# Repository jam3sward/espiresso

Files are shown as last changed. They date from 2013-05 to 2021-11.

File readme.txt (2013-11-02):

Starting the controller
-----------------------

sudo /etc/init.d/gaggia start

Stopping the controller
-----------------------

The halt button should be pushed to provide an opportunity for the PI to
shutdown before removing mains power.

sudo /etc/init.d/gaggia stop

Configuration files
-------------------

/etc/gaggia.conf

Data files
----------

Data is recorded to:
/var/log/gaggia/

Each run results in a new CSV (Comma Separated Values) file which is named
with the start date and time as follows:
YYMMDD-HHMM.csv

There is no upper limit on the number or size of these files, so they need
to be cleaned up manually. The files are fairly small (even if the machine
is left on for a couple of hours, the file would only be around 180kb).

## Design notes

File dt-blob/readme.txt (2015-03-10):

Step 1: check that Raspberry Pi firmware is later than July 15th 2014
---------------------------------------------------------------------

vcgencmd version

Step 2: install device tree compiler
------------------------------------

sudo apt-get update
sudo apt-get install device-tree-compiler

Step 3: edit the device tree source file as needed
--------------------------------------------------

nano dt-blob.dts

Step 4: compile the device tree source file to binary blob
----------------------------------------------------------

sudo dtc -I dts -O dtb -o /boot/dt-blob.bin dt-blob.dts

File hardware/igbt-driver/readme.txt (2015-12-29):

Eagle Schematic and Board files
The CAM files are in the pcb-cam-v1 folder

J.Ward
27/02/15

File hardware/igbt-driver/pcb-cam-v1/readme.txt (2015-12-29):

Es(pi)resso IGBT Driver

CAM files for PCB manufacture
Version: V1
Created: 27/02/15

These same files were used to successfully
manufacture a single prototype PCB here:
http://www.ragworm.eu

J.Ward
27/02/15

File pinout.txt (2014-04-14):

 3. GPIO2  = Button 1 (BUTTON1)
 5. GPIO3  = Button 2 (BUTTON2)
 7. GPIO4  = DS18B20 Thermometer (TEMPERATURE_BUS)
12. GPIO18 = SSR (SSR_OUT)
13. GPIO27 = Flow Sensor (FLOW_IN)
15. GPIO22 = Ultrasonic Ranger Echo In (RANGER_ECHO_IN)
16. GPIO23 = Ultrasonic Ranger Trigger Out (RANGER_TRIGGER_OUT)
18. GPIO24 = TSIC306 Temperature Sensor (TEMPERATURE_TSIC1)

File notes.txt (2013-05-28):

Running at startup
------------------
Created a script at:
/etc/init.d/gaggia

This starts automatically at boot, and stops at shutdown.

Manually start/stop as follows:
sudo /etc/init.d/gaggia start
sudo /etc/init.d/gaggia stop

Binary location
---------------
The binary is located here:
/usr/local/bin/gaggia

Logging
-------
Temperature logs are stored here:
/var/log/gaggia
Files are stored in CSV format.
File names are based on date and time.

Issues
------
* Time/date are incorrect when run from init.d (locale issue?)
* Discontinuous jumps in time stamps (probably due to NTP adjustment)

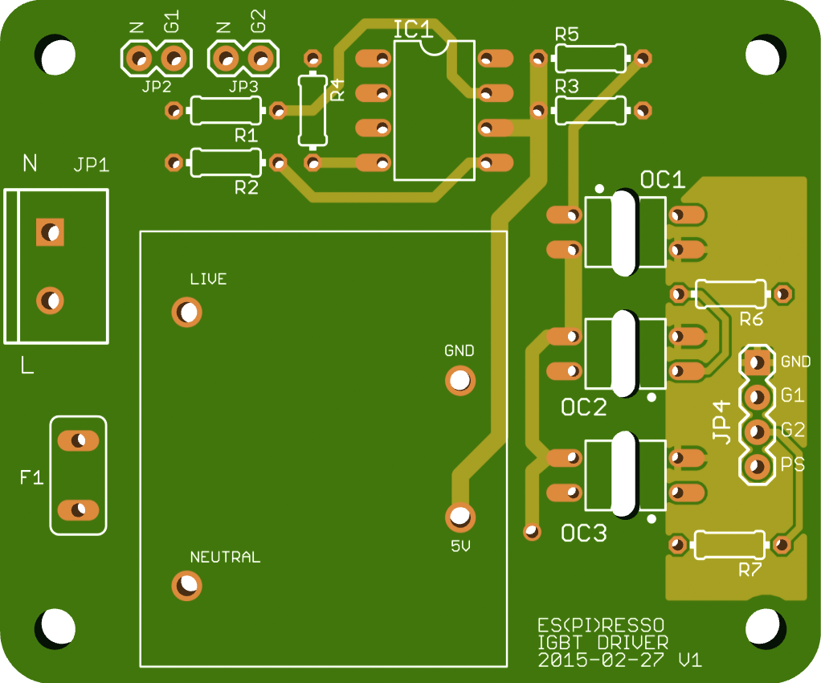
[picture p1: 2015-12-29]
hardware/igbt-driver/pcb-cam-v1/picture.png

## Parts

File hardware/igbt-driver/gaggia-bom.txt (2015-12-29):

Part Value           Device          Package             Description                              MF MPN OC_FARNELL OC_NEWARK
F1   1A              FUSETE5         TE5                 Fuse                                            unknown    unknown  
IC1  TC426           TC426           DIL08               1.5A Dual High-Speed Power MOSFET Driver                            
JP1  POWER           M025MM          SCREWTERMINAL-5MM-2 Standard 2-pin 0.1" header.                             
JP2  IGBT1           M02PTH          1X02                Standard 2-pin 0.1" header.                               
JP3  IGBT2           M02PTH          1X02                Standard 2-pin 0.1" header.                               
JP4  CONTROL         M04PTH          1X04                Standard 4-pin 0.1" header.                                                       
OC1  HCPL-817        TIL197          DIL04               TEXAS INSTRUMENTS OPTO COUPLER                  1683368    unknown  
OC2  HCPL-817        TIL197          DIL04               TEXAS INSTRUMENTS OPTO COUPLER                  1683368    unknown  
OC3  HCPL-817        TIL197          DIL04               TEXAS INSTRUMENTS OPTO COUPLER                  1683368    unknown  
R1   1K              R-EU_0204/7     0204/7              RESISTOR                                          
R2   1K              R-EU_0204/7     0204/7              RESISTOR                                         
R3   4K7             R-EU_0204/7     0204/7              RESISTOR                                           
R4   4K7             R-EU_0204/7     0204/7              RESISTOR                                           
R5   360R            R-EU_0204/7     0204/7              RESISTOR                                           
R6   270R            R-EU_0204/7     0204/7              RESISTOR                                           
R7   270R            R-EU_0204/7     0204/7              RESISTOR                                           
RG1  VTX-214-003-105 VTX-214-003-105 VTX-214-003         Vigortronix 90-265V AC to 5V DC 600mA

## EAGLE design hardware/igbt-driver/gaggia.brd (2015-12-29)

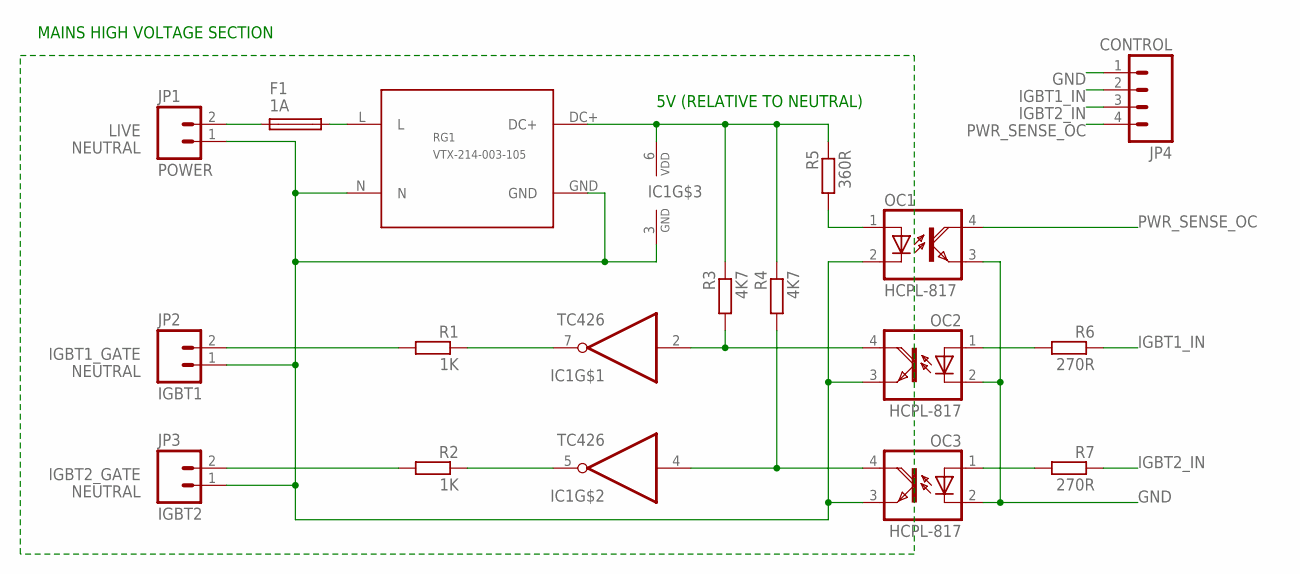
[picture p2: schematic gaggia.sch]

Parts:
F1: 1A; TE5
IC1: TC426; DIL08
JP1: POWER; SCREWTERMINAL-5MM-2
JP2: IGBT1; 1X02
JP3: IGBT2; 1X02
JP4: CONTROL; 1X04
OC1, OC2, OC3: HCPL-817; DIL04
R1, R2: 1K; 0204/7
R3, R4: 4K7; 0204/7
R5: 360R; 0204/7
R6, R7: 270R; 0204/7
RG1: VTX-214-003-105; VTX-214-003

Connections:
5V_NON_ISOLATED: IC1.6 (VDD), R3.1, R4.1, R5.1, RG1.DC+
GND: JP4.1, OC1.3 (EMI), OC2.2 (C), OC3.2 (C)
IGBT1_GATE: JP2.2, R1.2
IGBT1_IN: JP4.2, R6.1
IGBT2_GATE: JP3.2, R2.2
IGBT2_IN: JP4.3, R7.1
LIVE: F1.1, JP1.2
unnamed: IC1.4 (I), OC3.4 (COL), R4.2
unnamed: IC1.5 (O), R2.1
unnamed: OC3.1 (A), R7.2
unnamed: IC1.7 (O), R1.1
unnamed: OC1.1 (A), R5.2
unnamed: OC2.1 (A), R6.2
unnamed: IC1.2 (I), OC2.4 (COL), R3.2
unnamed: F1.2, RG1.L
NEUTRAL: IC1.3 (GND), JP1.1, JP2.1, JP3.1, OC1.2 (C), OC2.3 (EMI), OC3.3 (EMI), RG1.GND, RG1.N
PWR_SENSE_OC: JP4.4, OC1.4 (COL)

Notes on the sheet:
MAINS HIGH VOLTAGE SECTION
5V (RELATIVE TO NEUTRAL)

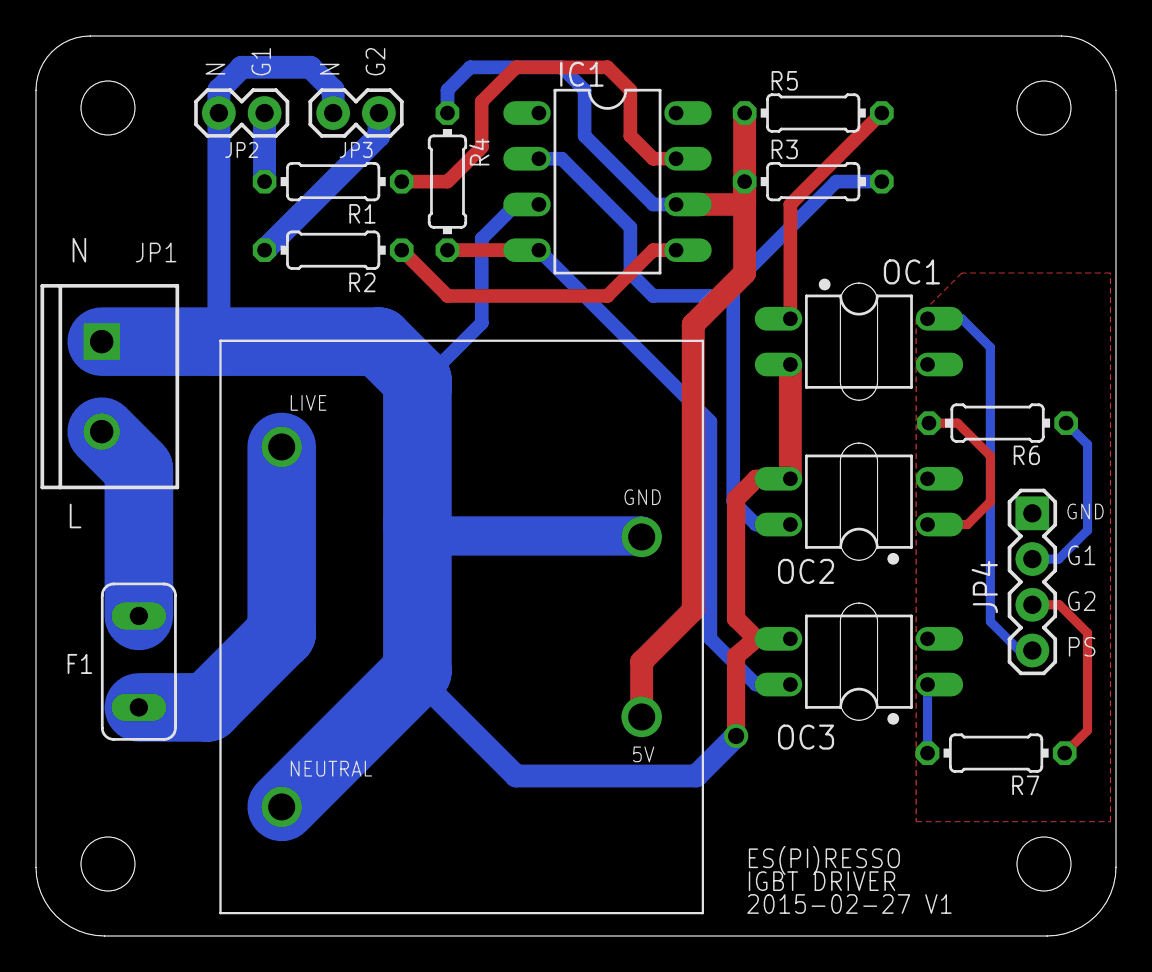
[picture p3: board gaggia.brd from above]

Board: 2 copper layers, 60.0 x 50.0 mm, 17 parts (0 on the bottom side), 17 nets.

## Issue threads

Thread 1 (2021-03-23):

Porting to the La Pavoni Puccino PCL

darkbasic, 2021-03-23:
Hi, first of all let me say "wow", you've put so much effort in this and ended up being such a great project!
I would like to port it to the La Pavoni Puccino PCL, but I'd like to start with the basics and eventually expand it later.
For the first iteration I'd like to implement only temperature control: no pump control, nor pressure, flow or water level.
I'm not a C++ developer (but I'm a Linux enthusiast) so I'll need some help to strip out the code base and test the individual pieces. Would you be willing to help me? I'm not sure if this is the right place to ask, but I didn't find any public email address.

jam3sward, 2021-03-24:
Thanks for the kind words!
Sure, would be happy to help with the odd question. The temperature control is where 99% of the benefit is to be had, so a good place to start!
Honestly speaking, although I implemented pump control and my machine can dispense a measured volume using its flow sensor... I still tend to just manually turn the pump on/off when pulling my morning shots :)
The water level sensor is really handy though, I find that really useful when topping up the machine.
I'm not sure how either of us can exchange e-mail addresses on here without exposing them to spammers, so I'm going to suggest you post on my blog here (which will reveal your e-mail address to me, then I can reply): http://int03.co.uk/blog/

darkbasic, 2021-03-24:
Awesome, I think I've managed to find your email address (and I've sent you an email), but I've also posted a comment to your blog just to be sure.

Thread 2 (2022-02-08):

Sorry, not an issue

SpeedGP, 2022-02-08:
Dude, you rock, this is crazy and exactly what I was looking for!!!

Any reason you're not running this on an Arduino instead? Seems like less can go wrong when you're not running a full OS.

Are you concerned about redundancy with the thermostat? I would like to see a temp fuse or is that what the pressure sensor is for? - pressure vessels scare the absolute crap out of me....

I'm planning a bare-bones mod, probably only PID and time monitoring. I think a scale mod of some sort would be cool, but probably difficult.

Thanks again for all of the time, dev, and love of coffee!!!

jam3sward, 2022-02-19:
Thanks for the kind words! Sorry it took a while to reply... I've only just spotted this.

I did consider Arduino, and it would be a good choice too. There are pros and cons of each, it depends how you plan to use it:
* Boot up time: Raspi takes a while to boot up, Arduino would be instant! (Arduino wins here)
* Remote access: Raspi means you can log in remotely, update the code over the network, have a Samba share with temperature/pressure logs... none of which is easy with Arduino. (Raspis wins here)
* I/O: sadly the Raspi has no analogue inputs, and needs an external ADC. The Arduino has plenty of course. (Arduino wins here)

So, if you don't care about being able to remotely log in and tinker with the code, or share logs on the network etc, then Arduino would be a very good choice of course!

Regarding redundancy with the thermostat, the Gaggia Classic has a thermal fuse (and it is still in circuit in my setup, as is the steam thermostat). So, if my temperature sensor fails or the software crashes, the first thing to open would be the steam thermostat. If the steam thermostat fails, the thermal fuse is next. So it has plenty of redundancy I would say.

Good luck with your project! The main benefit is the PID temperature control. That alone is enough to yield an amazing improvement in the quality of your espresso :)

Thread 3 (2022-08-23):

Boiler control

moosepr, 2022-08-23:
Hi there

I stumbled upon your project when looking into variable pressure control of coffee machine pumps and it's literally everything I had ever dreamed of! Truly fantastic work!

I would like to do something similar with an esp32 for brains, and was hoping i could make an all in one PCB to simplify the install.

I'm by no means an electrical engineer, but I can cut and paste a few circuits together with moderate success.

If you were doing it all again, would you use an IGBT to control the boiler as well as the pump? Your custom PCB has the spare channel available, it would be easy enough to add it in

Thanks

Pete

jam3sward, 2023-01-12:
I'm ashamed to reply to this after so long, but I just didn't see the notification!

Thanks for the kind words above, I'm pleased to hear that you found it helpful, and guess you must be well along with your ESP32 project by now :)

If I did this again, I would probably still use the SSR to switch the boiler, perhaps even the exact same model. There's so much thermal mass in the boiler and it is slow to react to input, so I think there is no advantage to high speed switching for that application and low speed PWM control is more than adequate to regulate boiler temperature.

On the other hand, I have come to think that the high speed IGBT switching of the pump is overkill and I would do that differently and more simply in a V2 design.

moosepr, 2023-01-20:
dont be ashamed!! its all good my project is still just an idea!!

I had been thinking of using a SSR for the pump, cycling it a few times a second would let you reduce the pressure without needing to get all precise with the cycle timing.

that being said, i was looking at making a custom pcb with it all baked in (not much space inside my machine) and pcb mounted SSR's are silly money!!

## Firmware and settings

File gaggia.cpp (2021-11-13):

#include <stdio.h>
#include <sched.h>
#include <ctype.h>
#include <signal.h>
#include <unistd.h>
#include <string>
#include <iostream>
#include <fstream>
#include <sstream>
#include <map>
#include <memory>

#include "timing.h"
#include "regulator.h"
#include "flow.h"
#include "pump.h"
#include "ranger.h"
#include "keyboard.h"
#include "inputs.h"
#include "system.h"
#include "display.h"
#include "adc.h"
#include "pressure.h"
#include "settings.h"
#include "pigpiomgr.h"
#include "network.h"

using namespace std;

//-----------------------------------------------------------------------------

static const string filePath( "/var/log/gaggia/" );
static const string configFile( "/etc/gaggia.conf" );

//-----------------------------------------------------------------------------

std::map<std::string, double> config;

bool g_enableBoiler = true;	///< Enable boiler if true
bool g_quit = false;		///< Should we quit?
bool g_halt = false;        ///< Should we halt? (shutdown the system)

double g_shotSize = 60.0;   ///< Shot size in ml

/// Automatic power off time in seconds. Zero disables the time out.
double g_autoPowerOff = 0.0;

class Hardware {
private:
    Timer       m_lastUsed;     ///< When was the last user interaction?
    ADC         m_adc;          ///< ADC used for buttons and pressure sensor
    Pump        m_pump;         ///< Pump controller
    Flow        m_flow;         ///< Flow sensor to measure volume dispensed
    Temperature m_temperature;  ///< Boiler temperature sensor
    Ranger      m_ranger;       ///< Range finder to measure water level
    Display     m_display;      ///< LCD display screen
    System      m_system;       ///< System information
    bool        m_pumpSense;    ///< Is the pump active?
    unsigned    m_pourCount;    ///< Pour count
    Timer       m_pourTime;     ///< Pour timer
    std::string m_networkIP;    ///< Primary network IP address

    std::shared_ptr<Regulator> m_regulator;

    std::shared_ptr<Inputs> m_inputs;

    std::shared_ptr<Pressure> m_pressure;

public:
    Timer & lastUsed() { return m_lastUsed; }

    ADC & adc() { return m_adc; }

    Pump & pump() { return m_pump; }

    Flow & flow() { return m_flow; }

    Temperature & temperature() { return m_temperature; }

    Ranger & ranger() { return m_ranger; }

    Display & display() { return m_display; }

    System & system() { return m_system; }

    Regulator & regulator() { return *m_regulator; }

    Inputs & inputs() { return *m_inputs; }

    Pressure & pressure() { return *m_pressure; }

    /// Returns true if the pump is active (whether enabled in software, or by
    /// using the manual front panel switch)
    bool pumpSense() const { return m_pumpSense; }

    /// Returns the pour counter value
    unsigned pourCount() const { return m_pourCount; }

    /// Returns the pour time in seconds
    double pourTime() const;

    /// Constructor
    Hardware() {
        // reset and stop the timer
        m_pourTime.reset().stop();

        // used to sense when pump is running
        m_pumpSense = false;

        // used to count how many times the pump has run
        m_pourCount = 0;

        // initialise ADC
        if ( !m_adc.open( I2C_DEVICE_PATH, ADS1015_ADC_I2C_ADDRESS ) )
            cerr << "gaggia: failed to open ADC\n";

        m_regulator = std::make_shared<Regulator>( m_temperature );
        m_inputs = std::make_shared<Inputs>( m_adc, ADC_BUTTON_CHANNEL );
        m_pressure = std::make_shared<Pressure>( m_adc, ADC_PRESSURE_CHANNEL );

        using namespace std::placeholders;

        // register button handler
        inputs().notifyRegister(
            std::bind( &Hardware::buttonHandler, this, _1, _2, _3 )
        );

        // register flow notification handler
        flow().notifyRegister(
            std::bind( &Hardware::flowHandler, this, _1 )
        );
    }

    /// Destructor
    virtual ~Hardware() {
        m_inputs.reset();
        m_regulator.reset();
        m_pressure.reset();
    }

    /// Called when buttons are pressed or released
    void buttonHandler(
        int button,     // button number (1,2)
        bool state,     // pressed (true) or released (false)
        double time     // time period since last state change
    );

    /// Called when notifications are received from the flow sensor
    void flowHandler( Flow::NotifyType type );

    /// Run the control loop
    int runController(
	    bool interactive,
	    const std::string & fileName
    );

    /// Run test mode
    int runTests();
};

//-----------------------------------------------------------------------------

void signalHandler( int signal )
{
	switch ( signal ) {
	case SIGINT:
		printf( "\ngaggia: received SIGINT\n" );
		g_quit = true;
		break;

	case SIGTERM:
		printf( "\ngaggia: received SIGTERM\n" );
		g_quit = true;
		break;
	}
}

//-----------------------------------------------------------------------------

double Hardware::pourTime() const
{
    return m_pourTime.getElapsed();
}

//-----------------------------------------------------------------------------

/// Called when buttons are pressed or released
void Hardware::buttonHandler(
    int button,     // button number (1,2)
    bool state,     // pressed (true) or released (false)
    double time     // time period since last state change
) {
    // reset the timer whenever the user interacts with the machine
    lastUsed().reset();

    switch ( button ) {
    case BREW_SWITCH:
        // brew switch pushed
        // When the front panel brew switch is pushed to enable the pump, this
        // will be triggered. Since we detect this from the 5V supply in the
        // pump modulation controller, there will be a delay in detecting when
        // the pump is switched off (because the reservoir capacitor in the 5V
        // supply takes time to discharge)
        cout << "gaggia: brew switch "
             << (state ? "enabled" : "disabled")
             << endl;

        // set or clear the flag (stores current state)
        m_pumpSense = state;

        // start or stop the pour timer
        if ( state )
            m_pourTime.start();
        else
            m_pourTime.stop();

        // if the power has been enabled, increment the pour counter
        if ( state ) ++m_pourCount;

        break;

    case BUTTON1:
        if ( state ) {
            // button 1 pushed

            // if the pump is idle
            if ( !pump().getState() ) {
                // ask the flow sensor to notify us after a shot
                // has been dispensed
                flow().notifyAfter( g_shotSize / 1000.0 );
                // turn on the pump
                pump().setState( true );
            } else {
                // pump is already running: turn it off
                pump().setState( false );
            }

            // display pump status for diagnostic purposes
            cout << "gaggia: pump "
                 << (pump().getState() ? "enabled" : "disabled")
                 << endl;
        } else {
            // button 1 released
        }
        break;

    case BUTTON2:
        if ( state ) {
            // button 2 pushed
        } else {
            // button 2 released
            if ( time >= 1.0 ) {
                // button was held for 1 second, shut down the system
                cout << "gaggia: shutting down\n";
                g_halt = true;
                g_quit = true;
            } else {
                // button was pushed briefly, toggle boiler power
                regulator().setPower( !regulator().getPower() );
                cout << "gaggia: boiler "
                     << (regulator().getPower() ? "enabled" : "disabled")
                     << endl;
            }
        }
        break;
    }
}

//-----------------------------------------------------------------------------

/// Called when notifications are received from the flow sensor
void Hardware::flowHandler( Flow::NotifyType type ) {
    // reset the timer when the pump is used (e.g. via front panel switch)
    lastUsed().reset();

	switch ( type ) {
	case Flow::Start :
		cout << "flow: started\n";
		break;

	case Flow::Stop  :
		cout << "flow: stopped\n";
		break;

	case Flow::Target:
		cout << "flow: target reached\n";
        // stop the pump
        pump().setState( false );
		break;
	}
}

//-----------------------------------------------------------------------------

/// very simplistic configuration file loader
bool loadConfig( std::string fileName )
{
	// open the file
	ifstream f( fileName.c_str() );
	if ( !f ) return false;

	do {
		// read key
		string key;
		f >> ws >> key;
		if ( !f ) break;

		// read value
		double value;
		f >> ws >> value;
		if ( !f ) break;

		// store key/value
		config[key] = value;
		//cout << key << " = " << value << endl;
	} while (true);

	f.close();

	return true;
}

//-----------------------------------------------------------------------------

std::string makeLogFileName()
{
	// get the time
	time_t now;
	time( &now );
	struct tm *info = localtime( &now );

	// format date and time into the filename
	char buffer[256];
	sprintf(
		buffer,
		"%02d%02d%02d-%02d%02d.csv",
		info->tm_year % 100,
		info->tm_mon+1,
		info->tm_mday,
		info->tm_hour,
		info->tm_min
	);

	// return the string
	return buffer;
}

//-----------------------------------------------------------------------------

int Hardware::runController(
	bool interactive,
	const std::string & fileName
) {
    // if button 2 is pushed during initialisation, abort
    if ( inputs().getButton(2) ) {
        cerr << "gaggia: button 2 is down: aborting" << endl;
        return 1;
    }

	// open log file
	ofstream out( fileName.c_str() );
	if ( !out ) {
		cerr << "error: unable to open log file " << fileName << endl;
		return 1;
	}

	// check that flow meter is available
	if ( !flow().ready() ) {
		out << "error: flow meter not ready\n";
		return 1;
	}

	// read configuration file
	if ( !loadConfig( configFile ) ) {
		out << "error: failed to load configuration from "
			<< configFile << endl;
		return 1;
	}

    // shot size in millilitres
    g_shotSize = config["shotSize"];

    // read auto cut out time (the value in the file is in minutes,
    // and we convert to seconds here)
    g_autoPowerOff = config["autoPowerOff"] * 60.0;

	// read PID controller parameters from configuration
	// these are the proportional, integral, derivate coefficients and
	// the integrator limits
	const double kP = config["kP"];
	const double kI = config["kI"];
	const double kD = config["kD"];
	const double kMin = config["iMin"];
	const double kMax = config["iMax"];

	// set the PID controller parameters
	regulator().setPIDGains( kP, kI, kD );
	regulator().setIntegratorLimits( kMin, kMax );

	// target temperature in degrees centigrade
	double targetTemp = config["targetTemp"];
	regulator().setTargetTemperature( targetTemp );

	// time step in seconds
	double timeStep = config["timeStep"];
	regulator().setTimeStep( timeStep );

    // pressure sensor calibration
    {
        // these are the multiplier and offset used to calibrate the analogue pressure
        // transducer measurement to match the front panel mechanical pressure gauge
        const double scale = config["pressureScale"];
        const double offset = config["pressureOffset"];
        pressure().setCorrection( scale, offset );
    }

	// output parameters to log
	char buffer[512];
	sprintf(
		buffer,
		"P=%.4lf,I=%.4lf,D=%.4lf,iMin=%.3lf,iMax=%.3lf,"
		"targetTemp=%.3lf,timeStep=%.3lf",
		kP, kI, kD, kMin, kMax,
		targetTemp, timeStep
	);
	out << buffer << endl;

	if ( interactive )
		nonblock(1);

	// time step for user interface / display
	const double timeStepGUI = 0.25;

	// start time and next time step
	double start = getClock();
	double next  = start;

	// turn on the power and start the regulator (boiler will begin to heat)
	regulator().setPower( g_enableBoiler ).start();

	do {
		// next time step
		next += timeStepGUI;

		// in interactive mode, exit if any key is pressed
		if ( interactive && kbhit() ) break;

		// if asked to stop (e.g. via SIGINT)
		if ( g_quit ) break;

		// calculate elapsed time
		double elapsed = getClock() - start;

		// get the latest temperature reading
		double latestTemp = regulator().getTemperature();

		// get the latest boiler power level
		double powerLevel = regulator().getPowerLevel();

		// number of millilitres of water drawn up by the pump
		double ml = 1000.0 * flow().getLitres();

        // pressure in Bar
        double bar = pressure().getBar();

        // pump status
        int pump = pumpSense() ? 1 : 0;

        // pour number (zero if the pump isn't running)
        int pour = (pump > 0) ? pourCount() : 0;

		// dump values to log file
		sprintf(
			buffer,
			"%.3lf,%.2lf,%.2lf,%.1lf,%.2lf,%d,%d",
			elapsed, powerLevel, latestTemp, ml, bar, pump, pour
		);
		out << buffer << endl;

		if (interactive) {
			printf( "%.2lf %.2lf %.1lf %.2lf %d\n", elapsed, latestTemp, ml, bar, pour );
		}

		// update temperature display
		display().updateTemperature( latestTemp );

        // update pressure display
        display().updatePressure( bar );

        // range measurement (convert to mm)
        double range = 1000.0 * ranger().getRange();

		// simplistic conversion to water level
		double minDist = 20.0;
		double maxDist = 100.0;
		range = std::max( minDist, std::min( range, maxDist ) );
		double level = 1.0 - (range - minDist) / (maxDist - minDist);

		// update water level display
		display().updateLevel( level );

        // update boiler power indicator
        display().setPowerOn( regulator().getPower() );

        // update pump status indicator
        display().setPumpOn( pumpSense() );

        // update time display
        display().updateTime( pourTime() );

        // update the network status display
        if ( m_networkIP.empty() ) {
            // query IP address (may return empty string)
            m_networkIP = getPrimaryIPString();

            // update the display (string may be empty)
            if ( !m_networkIP.empty() ) {
                display().setMessage( m_networkIP );
            } else {
                display().setMessage( "no network" );
            }
        }

        // if auto cut out is enabled (greater than one second) and if too
        // much time has elapsed since the last user interaction, and the
        // timer is running, turn off the boiler as a precaution
        if (
            (g_autoPowerOff > 1.0) &&
            lastUsed().isRunning() &&
            (lastUsed().getElapsed() > g_autoPowerOff)
        ) {
            // switch off the boiler
            regulator().setPower( false );

            // stop the timer to prevent repeat triggering
            lastUsed().stop();

            // explanatory message
            cout << "gaggia: switched off power due to inactivity\n";
        }

		// sleep for remainder of time step
		double remain = next - getClock();;
		if ( remain > 0.0 )
			delayms( static_cast<int>(1.0E3 * remain) );
	} while (true);

	if ( interactive )
		nonblock(0);

	// turn the boiler off before we exit
	regulator().setPower( false );

    // if the halt button was pushed, halt the system
    if ( g_halt ) {
        // rather than shutting down immediately, we want to schedule this to
        // happen a few seconds after our process has exited. here we use
        // bash to run a background job which will sleep for a few seconds
        // before powering off the system

        // format the command string (including time in seconds)
        const auto shutdownDelay = static_cast<int>(config["shutdownDelay"]);
        stringstream command;
        command << "bash -c \"sleep " << shutdownDelay << "; poweroff \" &";

        // execute the comamnd
        ::system( command.str().c_str() );
    }

    // exit normally
    cerr << "gaggia: exiting controller\n";
    return 0;
}

//-----------------------------------------------------------------------------

int Hardware::runTests()
{
    cout << "flow: " <<
        (flow().ready() ? "ready" : "not ready")
        << endl;

    double degrees = 0.0;
    cout << "temp: " <<
        ( temperature().getDegrees(degrees) ? "ready" : "not ready")
        << endl;

	cout << "range: " <<
		( ranger().initialise() ? "ready" : "not ready" )
		<< endl;

	flow().notifyAfter( g_shotSize / 1000.0 );

    nonblock(1);

	// time step
	const double timeStep = 0.5;

	// start time and next time step
	double start = getClock();
	double next  = start;

    do {
        // calculate next time step
        next += timeStep;

		// if quit has been requested (e.g. via SIGINT)
		if ( g_quit ) break;

        if ( kbhit() ) {
			// get key
			char key = getchar();

            if ( ( key >= '0' ) && ( key <= '9' ) ) {
                int value = key - '0';
                if ( value > 0 ) {
                    double duty = static_cast<double>(value) / 10.0;
                    pump().setPWMDuty( duty );
                    pump().setState( true );
                    cout << "pump duty = " << duty << endl;
                } else
                    pump().setState( false );
                continue;
            }

			bool stop = false;
			switch ( tolower(key) ) {
			case 'p':
                if ( !pump().getState() ) {
                    flow().notifyAfter( 60.0 / 1000.0 );
                }
                pump().setPWMDuty( 1.0 );
				pump().setState( !pump().getState() );
				cout << "pump: " << (pump().getState() ? "on" : "off") << endl;
				break;

            case 'r':
                {
                    double range = 0.0;
                    const int count = 50;
                    for (int i=0; i<count; ++i)
                        range += ranger().getRange() * 1000.0;
                    cout << "range average: "
                         << range / static_cast<double>(count) << endl;
                }
                break;

			default:
				stop = true;
			}

			if (stop) break;
		}

        // read temperature sensor
        double temp = 0.0;
        temperature().getDegrees( temp );

        // read core temperature
        double coreTemp = system().getCoreTemperature();

        // number of millilitres of water drawn up by the pump
        double ml = 1000.0 * flow().getLitres();

        // range measurement (convert to mm)
        double range = 1000.0 * ranger().getRange();

        // pressure measurement
        double bar = pressure().getBar();

        // print sensor values
        printf(
			"%.2lfC %.2lfC %.1lfml %.0lfmm %.1lf\n",
			temp, coreTemp, ml, range, bar
		);

		// update temperature on display
		display().updateTemperature( temp );

		// sleep for remainder of time step
		double remain = next - getClock();;
		if ( remain > 0.0 )
			delayms( static_cast<int>(1.0E3 * remain) );
    } while (true);

    nonblock(0);

	return 0;
}

//-----------------------------------------------------------------------------

int main( int argc, char **argv )
{
    // check that PIGPIO is initialised
    if ( !PIGPIOManager::get().ready() ) {
        cerr << "gaggia: failed to initialise PIGPIO\n";
        return 1;
    }

	// hook SIGINT so we can exit gracefully
	if ( signal(SIGINT, signalHandler) == SIG_ERR ) {
		cerr << "gaggia: failed to hook SIGINT\n";
		return 1;
	}

	// hook SIGTERM so we can exit gracefully
	if ( signal(SIGTERM, signalHandler) == SIG_ERR ) {
		cerr << "gaggia: failed to hook SIGTERM\n";
		return 1;
	}

    // ignore SIGHUP to prevent an exit when running as a systemd service
    // (this appears to be an issue with SDL_Init as others have reported
    // the same issue with SDL1 and PyGame)
    if ( signal(SIGHUP, SIG_IGN) == SIG_ERR ) {
        cerr << "gaggia: failed to hook SIGHUP\n";
        return 1;
    }

	if ( argc < 2 ) {
		cerr << "gaggia: expected a command\n";
		return 1;
	}

	const string command( argv[1] );

	bool interactive = false;

	for (int i=2; i<argc; ++i) {
		string option( argv[i] );
		if ( option == "-i" )
			interactive = true;
		else if ( option == "-d" ) {
            // disable the boiler
			g_enableBoiler = false;
		} else
			cerr << "gaggia: unexpected option\n";
	}

	if ( command == "stop" ) {
		Boiler boiler;
		boiler.powerOff();
		cout << "gaggia: turned off boiler SSR\n";
		return 0;
	} else if ( command == "start" ) {
		string fileName( makeLogFileName() );
		cout << "gaggia: starting controller (log=" << fileName << ")\n";
		return Hardware().runController( interactive, filePath + fileName );
	} else if ( command == "test" ) {
		cout << "gaggia: test mode\n";
		return Hardware().runTests();
	} else {
		cerr << "gaggia: unrecognised command (" << command << ")\n";
		return 1;
	}

	return 1;
}

//-----------------------------------------------------------------------------

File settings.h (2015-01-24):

#ifndef __settings_h
#define __settings_h

//-----------------------------------------------------------------------------

// GPIO pin used for Solid State Relay
// NOTE: this is now using hardware PWM
#define SSRPIN 18

// GPIO pin used for the Pump
#define PUMP_PIN 15
#define PUMP_PWM_PIN 14

// GPIO pin used by flow sensor
#define FLOWPIN 27

// GPIO pins used by ultrasonic ranger
#define RANGER_TRIGGER_OUT 23
#define RANGER_ECHO_IN 22

// GPIO pin used by the TSIC 306 temperature sensor
#define TSIC_PIN 24

// I2C directory path
#define I2C_DEVICE_PATH "/dev/i2c-1"

// ADS1015 ADC I2C address
#define ADS1015_ADC_I2C_ADDRESS 0x48

// ADC channel used by the button inputs
#define ADC_BUTTON_CHANNEL 0

// ADC channel used by the pressure sensor
#define ADC_PRESSURE_CHANNEL 1

// Maps logical button number to physical button number
// Where BUTTON1 is the top button on the panel, and the defined values
// correspond to the button numbers from the ADC
#define BUTTON1 3
#define BUTTON2 2
#define BREW_SWITCH 1

// Icon file paths
#define ICON_BOILER_POWER "/etc/gaggia/boiler_32x32.png"
#define ICON_PUMP_ACTIVE  "/etc/gaggia/pump_32x32.png"

//-----------------------------------------------------------------------------

#endif//__settings_h

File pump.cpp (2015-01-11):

#include "pump.h"
#include "settings.h"

//-----------------------------------------------------------------------------

Pump::Pump() :
	m_pump( PUMP_PIN ),
    m_pumpPWM( PUMP_PWM_PIN ),
	m_state( false )
{
	// Make the pin an output and drive it low
	m_pump.setOutput( true ).setState( false );

    // Make the pin an output and set the PWM frequency and duty
    m_pumpPWM.setOutput( true ).setPWMFrequency( 2000 ).setPWMDuty( 1.0 );
}

//-----------------------------------------------------------------------------

Pump::~Pump()
{
	// Turn off the pump
	m_pump.setState( false );
}

//-----------------------------------------------------------------------------

bool Pump::setState( bool state )
{
	m_pump.setState( state );
	m_state = state;
	return getState();
}

//-----------------------------------------------------------------------------

bool Pump::getState() const
{
	return m_state;
}

//-----------------------------------------------------------------------------

bool Pump::setPWMDuty( double duty )
{
    m_pumpPWM.setPWMDuty( duty );
    return true;
}

//-----------------------------------------------------------------------------

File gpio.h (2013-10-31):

#ifndef __gpio_h
#define __gpio_h

//-----------------------------------------------------------------------------

namespace BCM {

extern volatile unsigned *gpio;
extern volatile unsigned *pwm;
extern volatile unsigned *clk;

/// Open Broadcom peripheral interface
bool open();

/// Close Broadcom peripheral interface
void close();

} // namespace BCM

//-----------------------------------------------------------------------------

// GPIO setup macros. Always use INP_GPIO(x) before using OUT_GPIO(x) or
// SET_GPIO_ALT(x,y)
#define INP_GPIO(g) *(BCM::gpio+((g)/10)) &= ~(7<<(((g)%10)*3))
#define OUT_GPIO(g) *(BCM::gpio+((g)/10)) |=  (1<<(((g)%10)*3))
#define SET_GPIO_ALT(g,a) \
  *(BCM::gpio+(((g)/10))) |= (((a)<=3?(a)+4:(a)==4?3:2)<<(((g)%10)*3))

// set bits
#define GPIO_SET *(BCM::gpio+7)

// clear bits
#define GPIO_CLR *(BCM::gpio+10)

// read GPIO input bits 0-31
#define GPIO_IN0   *(BCM::gpio+13)

// pull up/pull down
#define GPIO_PULL   *(BCM::gpio+37)

// pull up/pull down clock
#define GPIO_PULLCLK0 *(BCM::gpio+38)

//-----------------------------------------------------------------------------

#endif//__gpio_h

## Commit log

2013-05-28 First import of Gaggia PID temperature controller for Raspberry Pi
2013-06-01 Changed PID parameters, added interactive mode and altered number of decimal places in output files.
2013-10-31 Modified to use hardware PWM, as yet untested.
2013-10-31 Added missing PWM files (forgot to commit previously)
    [pwm.cpp]
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2013-11-02 Fixed bug with improper boiler shutdown.
    [gaggia.cpp]
2013-11-02 Fixed SSR pin assignment used for hardware PWM. Added comments and assertion for documentation purposes.
    [pwm.cpp, settings.h]
2013-11-02 Settings are now read from a configuration file (sample file committed here) Added readme file with some more documentation
2013-11-23 Added Ranger class which implements support for the Ultrasonic Ranger Finder.
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2013-12-11 Implemented an interface class for the water flow sensor. Tested and apparently working.
2013-12-11 Flow sensor can now measure in litres. Performed basic calibration using digital scales with the sensor in situ on the Gaggia machine.
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2013-12-13 The flow sensor can now send an asynchronous notification when a specified volume of water has been pumped.
2014-02-11 Modified GPIO pins for new hardware. Removed references to halt button. Added new system class which allows core temperature to be queried. Added test mode which displays sensor data.
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2014-02-11 Modified Ranger to sample on separate thread, to avoid blocking. It attempts to remove outliers (with limited success) and low pass filters data.
    [gaggia.cpp]
2014-02-11 Added control of Pump (press P key during test mode to toggle on/off).
2014-02-11 Added support for button inputs (not yet working, assumed due to clash with BCM IO functions).
2014-02-12 Fixed a bug with missing call to BCM::open() in PWM ctor. Rewrote Temperature class to use w1-therm module. Fixed a bug in GPIOPin::getState() which failed to rewind file before reading.
    [gaggia.cpp, gpiopin.cpp, pwm.cpp]
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2014-02-16 Added basic water level indication (doesn't work all that well). Added graceful shutdown on receipt of SIGINT and SIGTERM.
    [gaggia.cpp]
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2014-02-20 Extended Flow class to send notifications when flow starts, stops or reaches target volume. Added simple code to gaggia.cpp to test this new functionality.
2014-02-28 Started refactoring temperature control loop into a separate Regulator class. This will eventually allow the user interface thread to run independently.
2014-03-01 Refactored to use the new Regulator class to manage temperature. Added methods to Regulator to read current boiler power level.
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2014-04-20 Modified range finder to use HC-SR04 kernel module instead of polling the sensor from user mode.
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2014-04-21 Water level indicator now uses 20-100mm range, based on measurements in situ. Pump test function now dispenses 60ml. Added range test which reports an average of 50 readings. Introduced 250ms delay i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
2014-04-21 Button 1 now dispenses a measured shot, using the flow sensor. The pump can be stopped by a second button push. Pressing button 2 briefly toggles the boiler power. Pressing button 2 for 1 second shut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
2014-04-24 Added missing mutex to inputs.h and inputs.cpp
    [inputs.cpp]
2014-04-29 Added safe mode: if button 2 is held during start up, the controller will exit. This is useful when you want to SSH into the machine without starting up the boiler.
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2014-04-30 Increased poll timeout for flow sensor to 1 second, to reduce overhead. Fixed bug with pump being turned off in test loop.
    [gaggia.cpp]
2014-07-14 Added automatic power off function, to shut down the boiler if the machine is left for a long period without any user input. This is configured with the autoPowerOff setting in the configuration file.
2014-07-19 Reset the g_lastUsed timer when the pump is used via the front panel switch.
    [gaggia.cpp]
2015-01-03 Added preliminary code to interface with ADS1015 ADC. This has been tested separately but not yet integrated.
2015-01-03 The ADC is now used to read the state of both front panel buttons through a single analogue input, using a resistor ladder.
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2015-01-04 Modified Ranger class to use HCSR04 class instead of kernel mode driver
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2015-01-06 Modified to use PIGPIOD for the majority of the GPIO. Moved static variables into class. Partially tested and working in test mode (not yet tested controller or PWM). Temperature, Ranger, Flow sensor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
2015-01-09 Added support for pressure sensor. Although not yet calibrated, it seems reasonably consistent with the front panel pressure gauge.
2015-01-11 Added a mutex to ADC::getVoltage to allow simultaneous access from the threads used to process button inputs (Input) and pressure sensor readings (Pressure). Modified GPIOPin class to return the last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
2015-01-11 Added Raspberry Pi device tree source file from August 1st 2014 firmware, with the idea of modifying this to set the initial power up state of the GPIO pins.
2015-01-11 Configured pump GPIO pins as inputs with pull-down at boot time, to prevent it being enabled as the system boots.
2015-01-11 Made the pump PWM duty default to 100% to allow manual use of the machine without pump modulation. Added test code for the brew switch power detect (working!) Added logging of pressure sensor measure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
2015-01-12 Fixed typo in comment
    [tsic.cpp]
2015-01-12 Fixed a bug with reporting flow start/stop events, due to incorrect timeout introduced when the code was changed to use PIGPIO.
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2015-01-17 More rigorous checking of pulse widths for TSIC temperature sensor, and pull up configuration, in an attempt to improve robustness against spikes.
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2015-01-24 Now keeps track of the number of times the pump has been run (pours)
2015-01-29 Fixed bug with TSIC code. Increased timing tolerance in an attempt to improve robustness. Renamed variables to make code more comprehensible.
    [tsic.cpp]
2015-01-29 Use an average of 3 ADC samples for pressure sensor readings, to compensate for jitter due to EP5 vibration pump.
    [pressure.cpp]
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2015-03-10 Added shot timer, which displays elapsed time in seconds during a shot. Currently based on pump power sense output (therefore runs on slightly).
2015-06-07 Added pressure transducer calibration (scale and offset). These can be used to adjust the analogue pressure sensor readings to match the mechanical pressure gauge.
2015-12-12 Aded includes to fix compilation issues after OS upgrade
    [adc.cpp, hcsr04.cpp]
2015-12-29 Added device tree overlay to ensure GPIO pins used by pump are low at first boot
2015-12-29 Added an updated dt-blob.dts (original Raspberry Pi version), prior to making the required changes, which I'll do in a second commit.
2015-12-29 Changes to ensure that GPIO 14 and 15 used by the pump are low on first boot
2015-12-29 Changed halt to poweroff (fix issue with not powering down since update of Raspbian)
    [gaggia.cpp]
2015-12-29 Started adding hardware and PCB design files
    [gaggia.brd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]
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2020-11-16 Power off now occurs after process exit, allowing shutdown messages to be viewed on console.
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

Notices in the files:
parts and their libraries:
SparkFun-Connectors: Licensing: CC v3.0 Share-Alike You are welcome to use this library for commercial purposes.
